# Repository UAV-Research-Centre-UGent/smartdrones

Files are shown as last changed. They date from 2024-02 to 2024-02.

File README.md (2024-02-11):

# Smartdrones
Smartdrone is an innovative UAV platform that redefines drone capabilities in educational and research settings by integrating a smartphone as the onboard computer for the drone's self-guided navigation. This approach enhances the drone's functionality not only by utilizing advanced cameras and sensors present on modern smartphones but also by taking advantage of the vast programming libraries and communication protocols available for smartphones. 

## Main features
* **Affordable:** Our design emphasizes cost-effectiveness, utilizing affordable, readily available electronic components and hardware. 
* **Open:** The platform is open and free to use. It utilizes open-source hardware and firmware. 
* **Extensible:** It is easy to integrate with various types of smartphones and sensors, ensuring adaptability to future requirements and advancements.

## Smartdrone´s architecture
Our system has three key parts: 1) The Autonomous Navigation Block (ANB) for self-flying, 2) The Manual Navigation Block (MNB) for flying it by hand using a radio, and 3) The Flight Controller Block (FCB) which manages the drone's flying mechanisms. The FCB uses sensor data to control the motors. The ANB makes the drone fly on its own using a smartphone's sensors and apps. The MNB lets a person take manual control takeover through a radio transmitter.

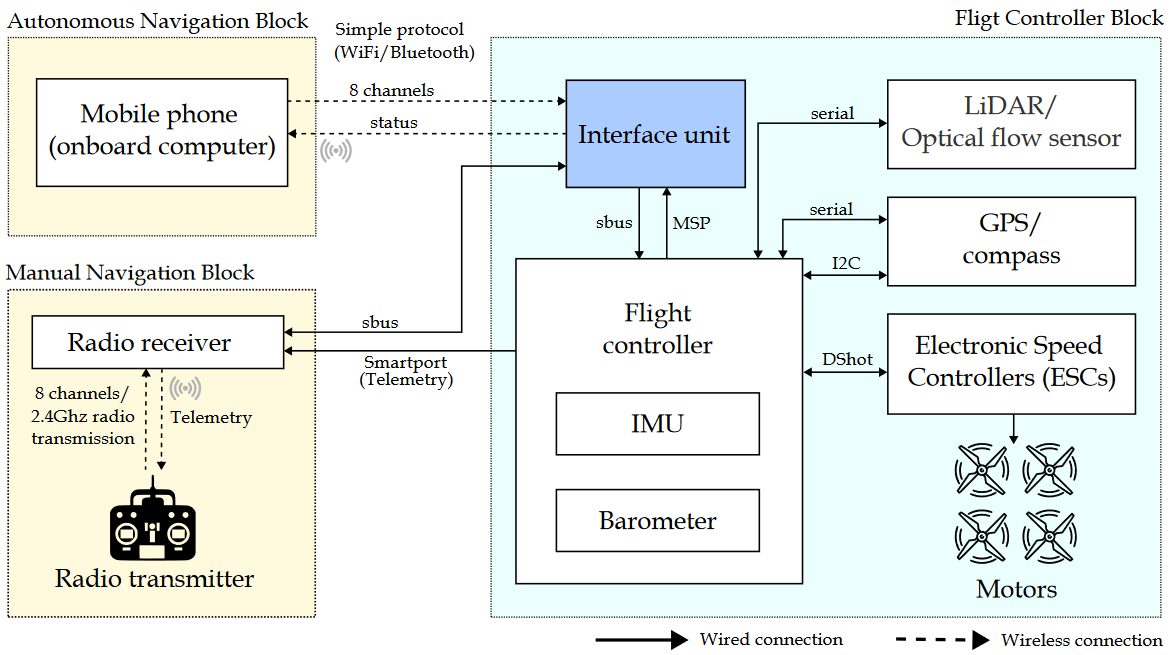
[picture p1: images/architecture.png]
Smartdone architecture


## Getting started
### Build the drone
Choose the right frame for your project. Each frame comes with recommended components, but keep in mind that not all suggested parts might be available or exactly the same. The key is to ensure that the components you select serve the same purpose or function. The folder with available frames is located in [/frames](https://github.com/UAV-Research-Centre-UGent/smartdrones/tree/main/frames). This folder contains the files for cutting the parts in carbon fiber and 3D parts that should be printed in TPU (or similar flexible filament) and PETG (or similar filament). It also provides the pins used for soldering the connections. Below is an overview of the pin connections of all the components.

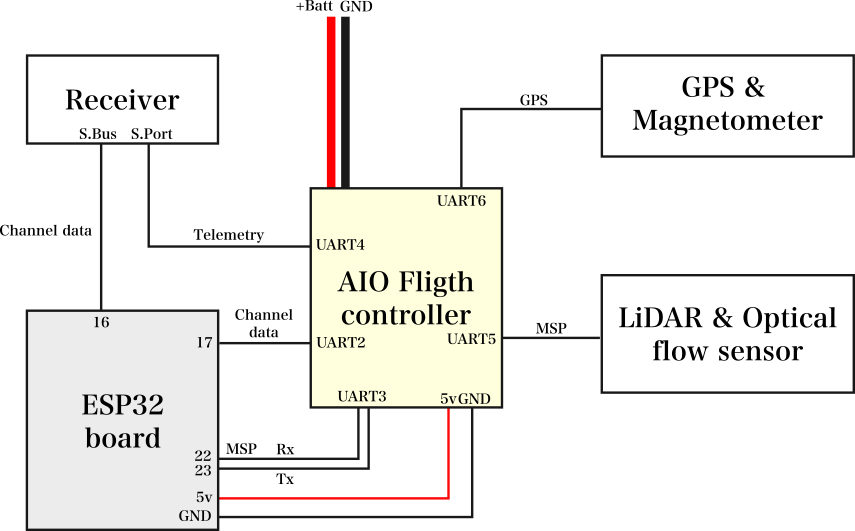
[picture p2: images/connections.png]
Connections


### Configure the drone
After installing iNAV on the flight controller, it needs to be set up correctly. The setup can vary based on the components and ports (pins) chosen on the flight controller. You'll find a document named setup.docx in the frame's folder, which explains the flight controller's configuration in detail. Below, we provide an overview of the general configuration settings.
* Ports configuration:
  * UART2: Serial (receiver)
  * UART3: MSP active (ESP32)
  * UART4: Telemetry port. Smartport.
  * UART5: MSP. Range finder and optical flow.
  * UART6: GPS.
* Receiver setup:
  * Map: TEAR.
* Modes:
  * ARM: Channel 5. Active when it is higher than 1500.
  * HORIZON, NAV ALTHOLD, NAV POSHOLD. Active when it is higher than 1500 (default).
  * BEEPER: Channel 7. Active when it is higher than 1500. 

### Transmitter
To utilize the platform, you need to pair the receiver with a compatible transmitter. The platform is compatible and has been tested with the following transmitters:
* TX16S Radio Controller (4-in-1)
* Zorro Radio Controller (4-in-1)

The basic setup is outlined below:
* Map: TEAR
* Channel 1: Throttle (THR)
* Channel 2: Elevator (ELE)
* Channel 3: Aileron (AIL)
* Channel 4: Rudder (RUD)
* Assign Channel 5 (ARM), Channel 6 (Flight Modes), Channel 7 (Enable Autonomous), and Channel 8 (Buzzer) to any available fixed switch.

### Test the drone
After setting up the drone, the next step is to conduct a test flight. This helps check if all components are correctly installed and configured and if the drone flies well. To test Smartdrones, two primary firmware options are available for installation on the ESP32.
1. [PassThrough](https://github.com/UAV-Research-Centre-UGent/smartdrones/tree/main/firmware/PassThrough): This firmware relays control commands directly from the transmitter to the drone.
2. [SimpleAutonomous](https://github.com/UAV-Research-Centre-UGent/smartdrones/tree/main/firmware/SimpleAutonomous): This firmware allows the drone to receive simple text commands from a smartphone through Bluetooth. The smartphone connects to the ESP32 via Bluetooth, sending commands that specify joystick positions and channels for basic movements.

### Tunning
While the configuration document includes recommended iNav PID settings, keep in mind these values vary for each drone. If the drone vibrates too much or is unstable during flight, you can adjust its performance by modifying the PID values. For guidance on how to do this, check out the video playlist at: [iNAV configuration guide](https://www.youtube.com/playlist?list=PLOUQ8o2_nCLloACrA6f1_daCjhqY2x0fB).

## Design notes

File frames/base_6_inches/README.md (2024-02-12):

# Base frame (5-6 inches)
This frame is designed to carry out smartphones with screen sizes up to 6.5 inches. When assembled with the suggested components and powered by a 2000 mAh 4S battery, the drone is able to achieve a flight duration ranging from 10 to 15 minutes.

## Components
This is the list of recommended components. 
- [GOKU HD 745 EVO 40A AIO](https://flywoo.net/products/goku-hd745-evo-40a-aio-bl_32-dji-plus-play)
- [iFlight M8Q-5883-GPS Module V2.0](https://newbeedrone.com/products/iflight-m8q-5883-gps-and-compass-v2-0)
- [Matek 3901-L0X](http://www.mateksys.com/?portfolio=3901-l0x)
- [FrSky R-XSR](https://www.frsky-rc.com/product/r-xsr/)
- [T-Motor F2203.5 - 1500KV](https://store.tmotor.com/product/f2203_5-fpv-motor.html) 
- [ESP32 Development Board](https://www.espressif.com/en/products/devkits/esp32-devkitc)
- [Gemfan F6030](https://www.getfpv.com/gemfan-floppy-proppy-f6030-3-blade-propeller-set-of-4.html)

## Assembly the frame
The drone construction is based on a carbon fiber Frame, which is fastened using screws, secure nuts, and aluminum standoffs. The design files for each carbon fiber part can be found in the [frame](frame) folder, provided in DXF format for precision manufacturing. Below is a detailed breakdown of the parts that constitute the frame, including the thickness of each carbon fiber component:
* Top Plate: 1.5mm thick
* Bottom Plate: 2mm thick
* Front Arm: 6mm thick
* Rear Arm: 6mm thick
* Arm Holder: 2mm thick
* Aluminum Standoffs: 25mm in length
* M3 Bolts and Nuts: 12mm in size

An illustrative guide detailing the assembly of the frame is provided in the image below. 
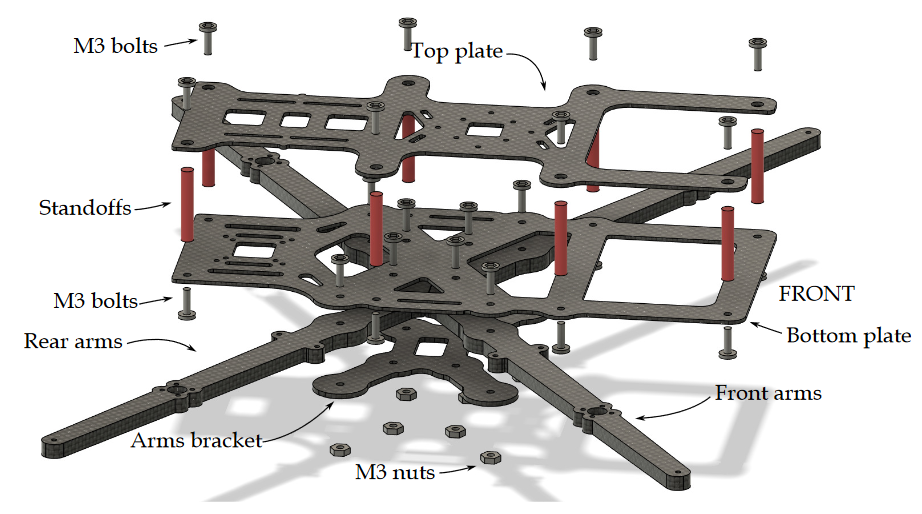
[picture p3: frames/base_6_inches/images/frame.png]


## 3D printed parts
The drone frame includes parts that need to be printed using a 3D printer. The files for these specific parts are in the [3dparts](3dparts) folder. Below, we provide a detailed list of the components to be printed, along with the recommended type of filament for each. 
* [Front bumper](3dparts/tpu-front_bumper.stl) (TPU-95-98A) 
* [Landing foot](3dparts/tpu-landing_foot.stl) (TPU-95-98A)
* [Battery holder](3dparts/tpu-battery_holder.stl) (TPU-95-98A)
* [LiDAR mount](3dparts/tpu-lidar_mount.stl) (TPU-95-98A)
* [Antenna holder (left)](3dparts/tpu-antenna_holder_left.stl) (TPU-95-98A)
* [Antenna holder (right)](3dparts/tpu-antenna_holder_right.stl) (TPU-95-98A)
* [Antenna tip](3dparts/tpu-antenna_tip.stl) (TPU-95-98A)
* [ESP32 holder](3dparts/petg-esp32_holder.stl) (PETG)
* [Flight controller protector](3dparts/petg-fc_protector.stl) (PETG)
* [Front duct (left)](3dparts/petg-duct_front_left.stl) (PETG)
* [Front duct (right)](3dparts/petg-duct_front_right.stl) (PETG)
* [Rear duct (left)](3dparts/petg-duct_rear_left.stl) (PETG)
* [Rear duct (left)](3dparts/petg-duct_rear_right.stl) (PETG)

The location of the 3D printed parts are shown in the following image: 
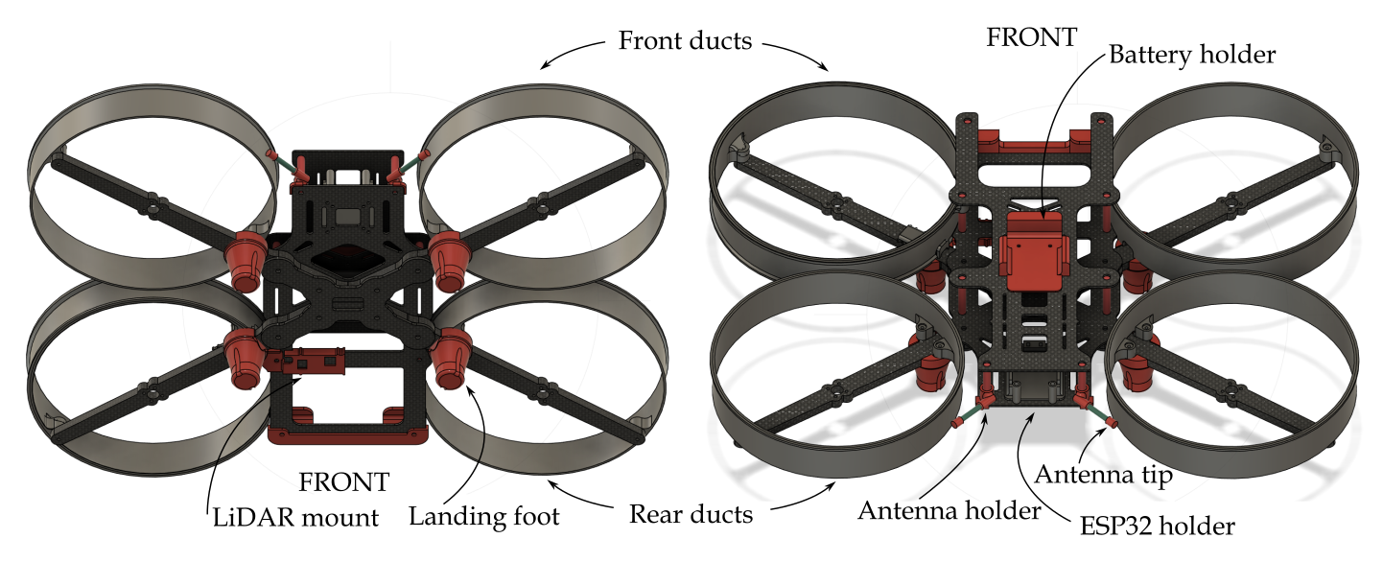
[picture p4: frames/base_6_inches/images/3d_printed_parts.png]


In addition to the parts already mentioned, your drone build will require some additional components and hardware not previously listed. These include 20mm M2 screws and nuts, which are used for securing the ducts. You will also need battery straps to ensure both the smartphone and the battery are firmly held in place.

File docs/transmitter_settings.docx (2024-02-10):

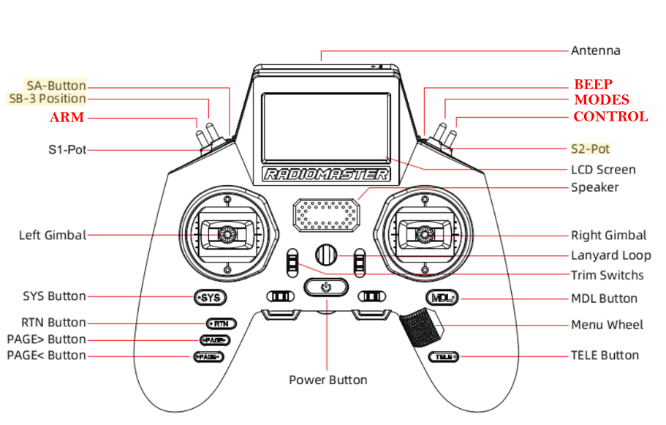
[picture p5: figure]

Cheat sheet

THROTTLE (T) | Channel 1
PITCH | Channel 2
ROLL | Channel 3
YAW | Channel 4
ARM | Channel 5 | Arm the drone
MODES | Channel 6 | Change the modes
CTRL | Channel 7 | Leave/take control (do not used by iNAV)
BEEP | Channel 8 | Beeping

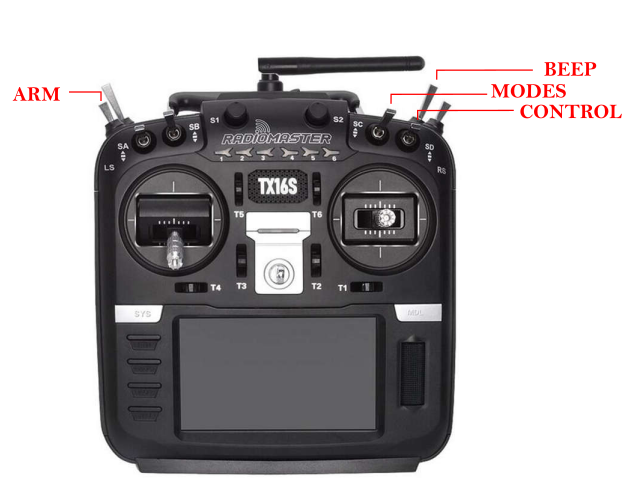
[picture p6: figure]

Values for channels

MIN_SBUS_VALUE | 172
MAX_SBUS_VALUE | 1811
MID_SBUS_VALUE | 992

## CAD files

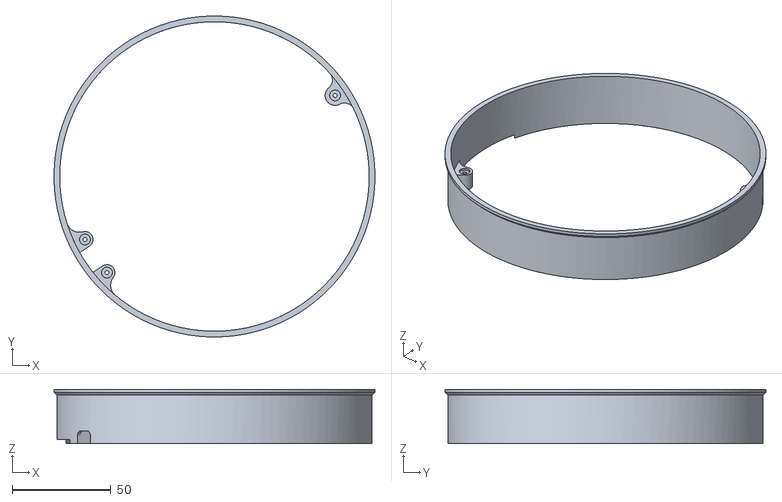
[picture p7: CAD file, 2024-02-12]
frames/base_6_inches/3dparts/petg-duct_front_right.stl
162.2 x 162.2 x 27.5

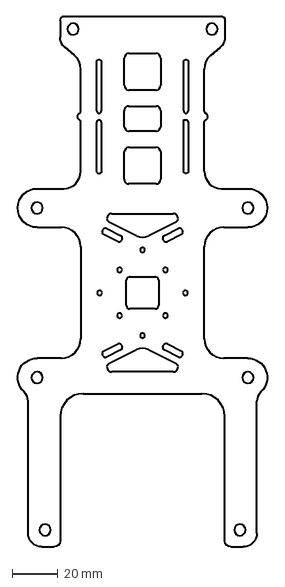
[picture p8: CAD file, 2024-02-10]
frames/base_6_inches/frame/top_plate.dxf
110.4 x 232.0 mm

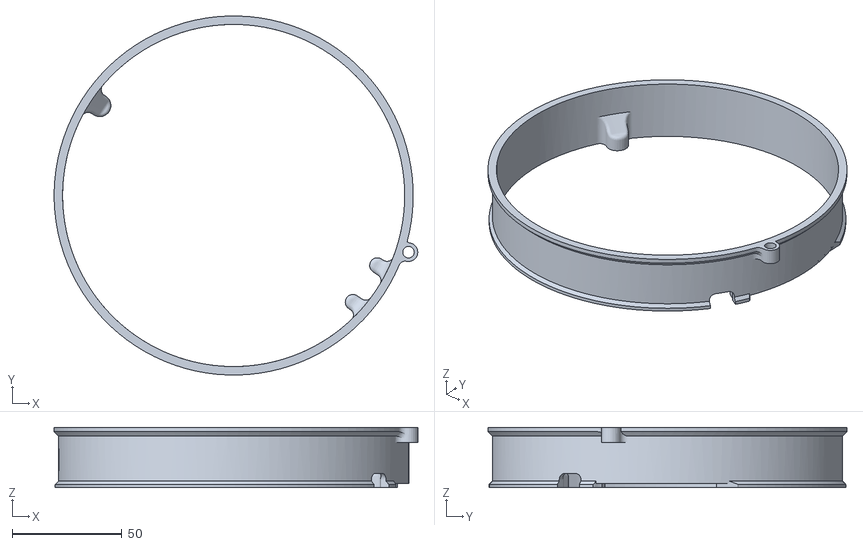
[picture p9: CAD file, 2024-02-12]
frames/base_6_inches/3dparts/petg-duct_front_left.stl
165.6 x 163.5 x 27.5

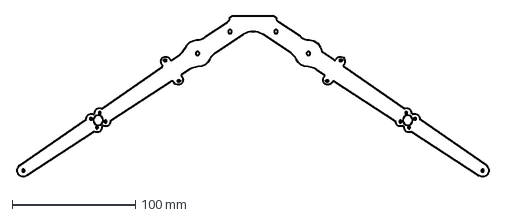
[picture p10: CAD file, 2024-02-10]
frames/base_6_inches/frame/front_arm.dxf
384.6 x 130.9 mm

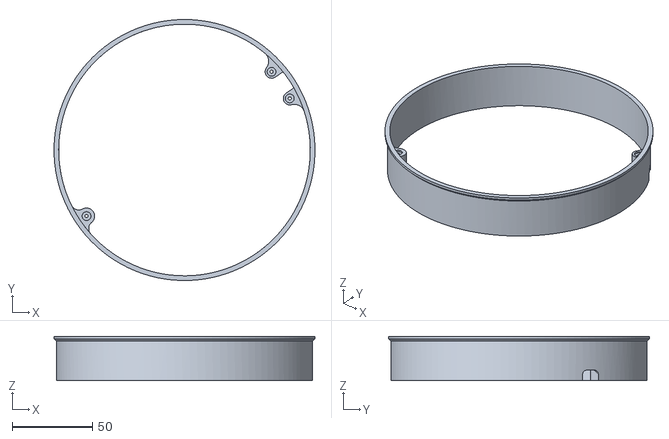
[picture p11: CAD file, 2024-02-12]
frames/base_6_inches/3dparts/petg-duct_rear_left.stl
162.2 x 162.2 x 27.5

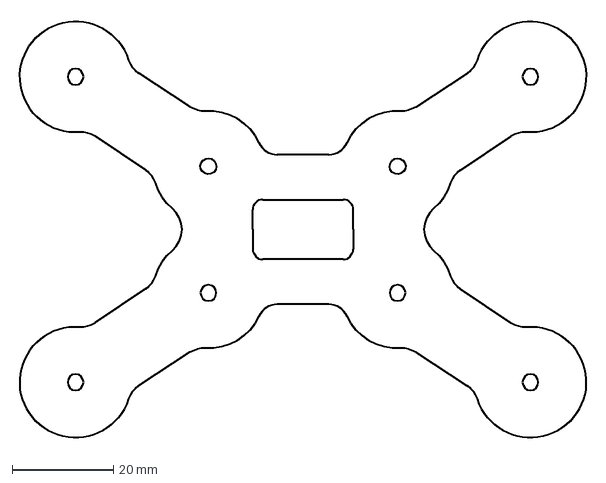
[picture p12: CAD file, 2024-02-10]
frames/base_6_inches/frame/arm_holder.dxf
113.5 x 84.5 mm

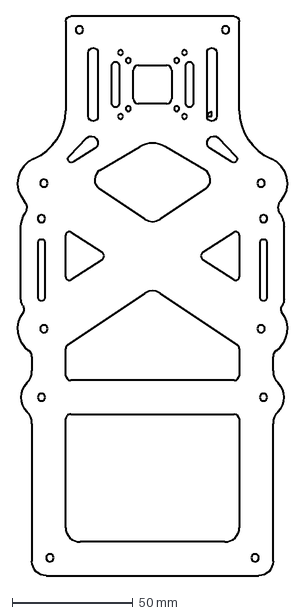
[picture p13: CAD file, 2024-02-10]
frames/base_6_inches/frame/bottom_plate.dxf
113.0 x 232.0 mm

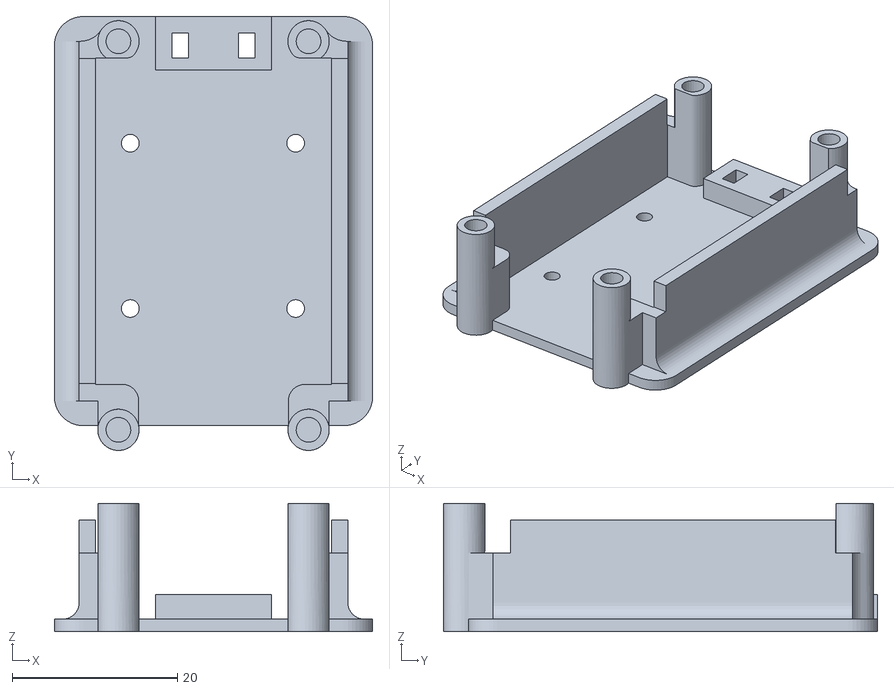
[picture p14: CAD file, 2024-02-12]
frames/base_6_inches/3dparts/petg-esp32_holder.stl
38.5 x 52.5 x 15.5

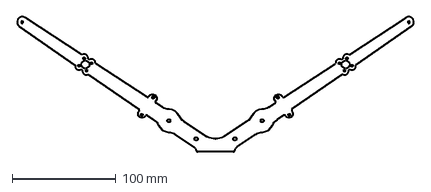
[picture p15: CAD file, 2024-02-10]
frames/base_6_inches/frame/rear_arm.dxf
384.6 x 130.9 mm

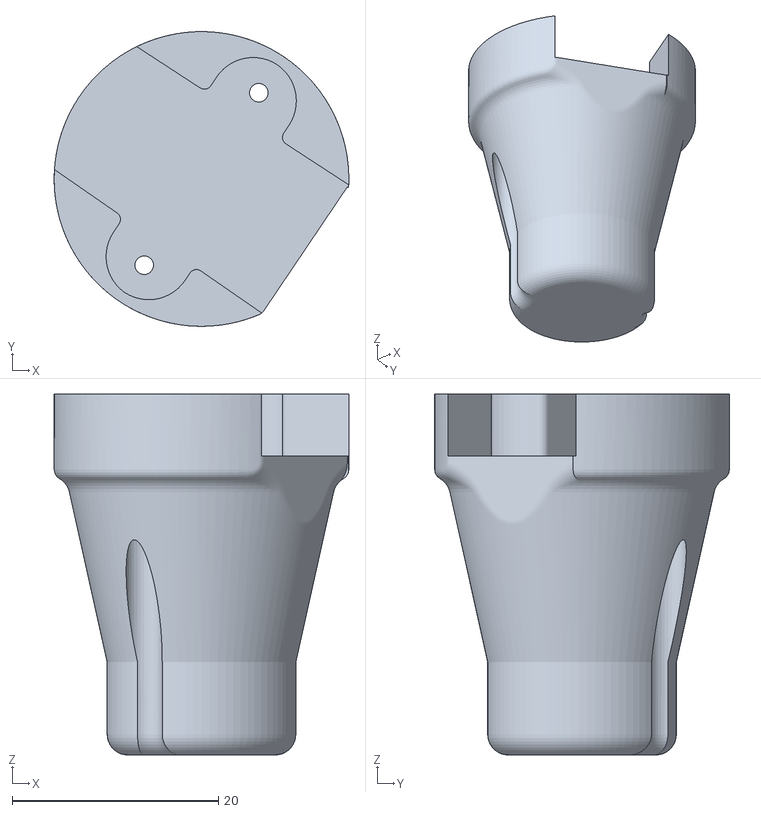
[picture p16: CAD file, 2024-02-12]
frames/base_6_inches/3dparts/tpu-landing_foot.stl
28.6 x 28.6 x 35.0

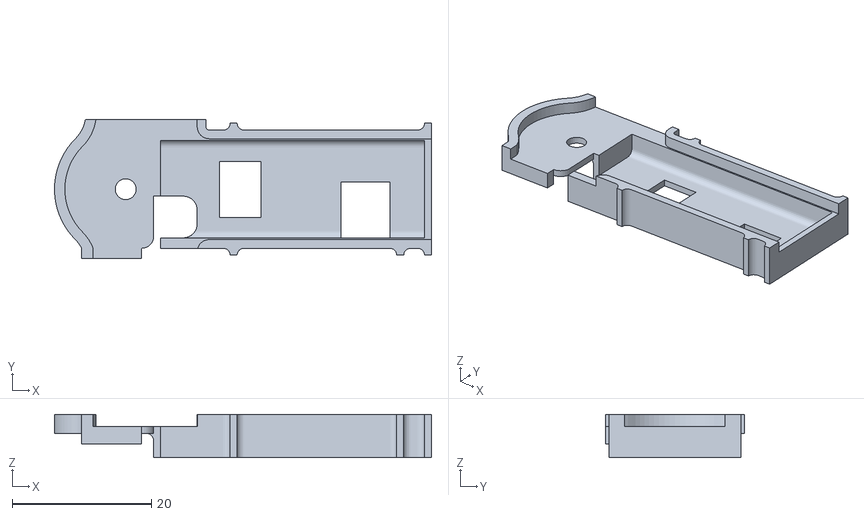
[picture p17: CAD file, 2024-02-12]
frames/base_6_inches/3dparts/tpu-lidar_mount.stl
54.2 x 20.1 x 6.25

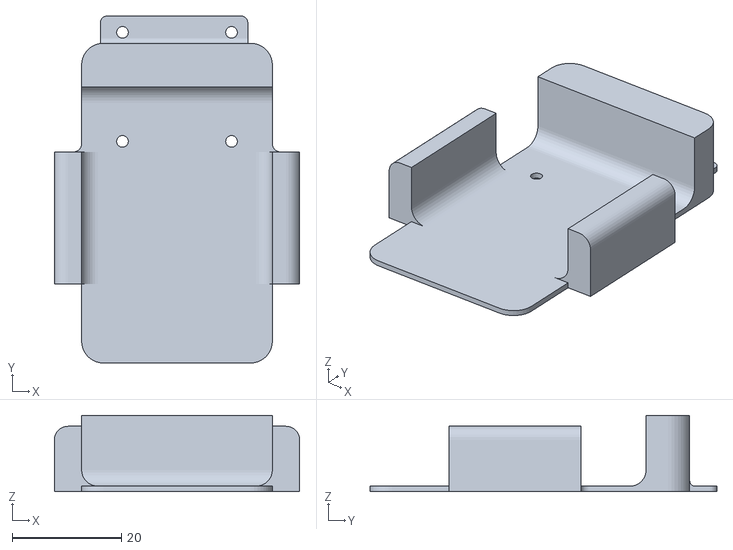
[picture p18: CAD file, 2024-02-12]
frames/base_6_inches/3dparts/tpu-battery_holder.stl
45.0 x 63.6 x 14.0

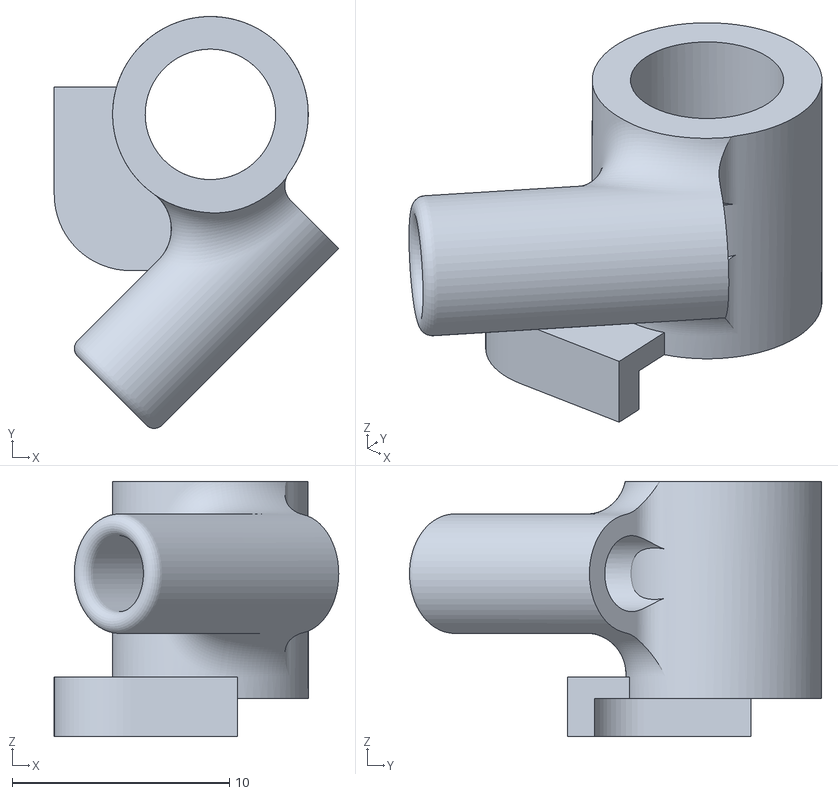
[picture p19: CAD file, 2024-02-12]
frames/base_6_inches/3dparts/tpu-antenna_holder_left.stl
13.1 x 18.9 x 11.8

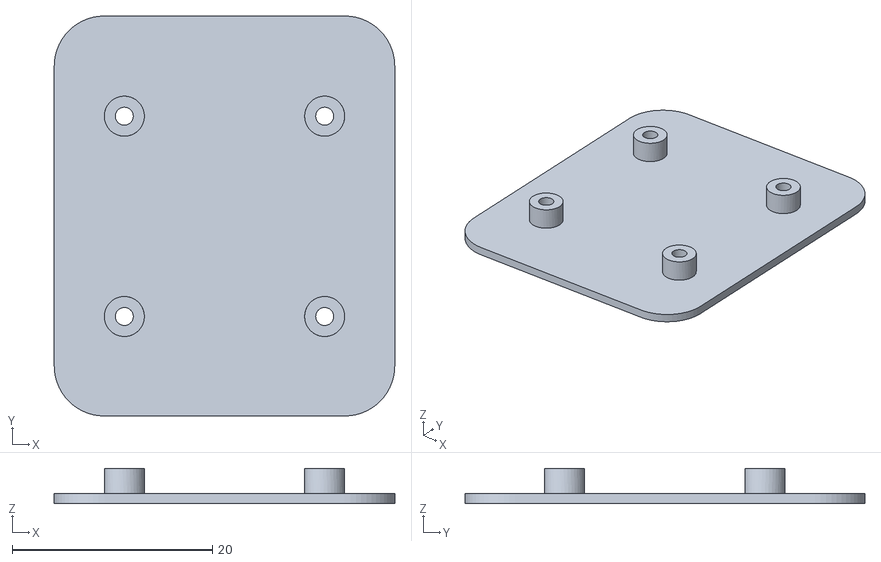
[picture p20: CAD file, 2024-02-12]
frames/base_6_inches/3dparts/petg-fc_protector.stl
34.0 x 39.9 x 3.50

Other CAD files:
frames/base_6_inches/3dparts/petg-duct_rear_right.stl
frames/base_6_inches/3dparts/tpu-antenna_holder_right.stl
frames/base_6_inches/3dparts/tpu-front_bumper.stl
frames/base_6_inches/3dparts/tpu-antenna_tip.stl

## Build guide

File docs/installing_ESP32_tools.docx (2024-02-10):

# Installing ESP32 Add-on in Arduino IDE

To install the ESP32 board in your Arduino IDE, follow these next instructions:

In your Arduino IDE, go to File> Preferences

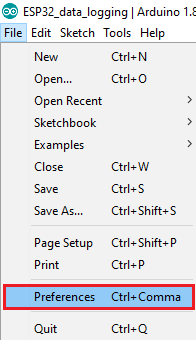
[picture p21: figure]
Installing ESP32 Add-on in Arduino IDE Windows, Mac OS X, Linux open preferences

Enter https://dl.espressif.com/dl/package_esp32_index.json into the “Additional Board Manager URLs” field as shown in the figure below. Then, click the “OK” button:

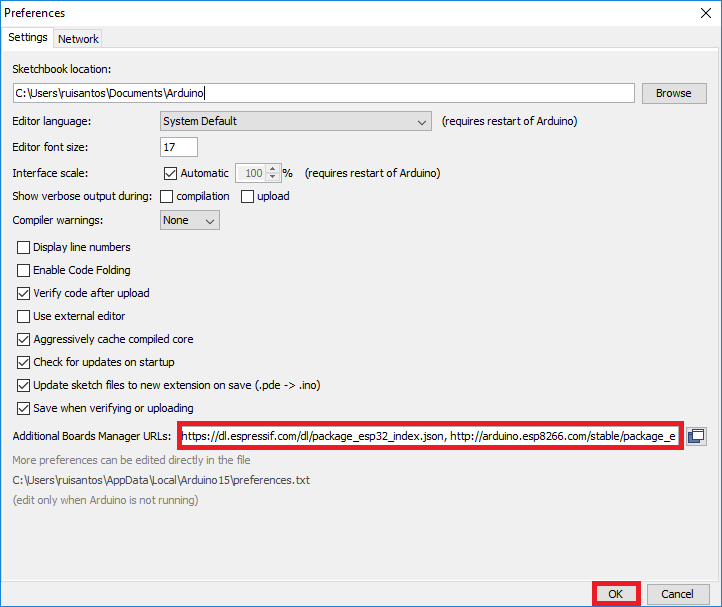
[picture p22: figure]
Installing ESP32 Add-on in Arduino IDE Windows, Mac OS X, Linux enter URLs

Note: if you already have the ESP8266 boards URL, you can separate the URLs with a comma as follows:

https://dl.espressif.com/dl/package_esp32_index.json, http://arduino.esp8266.com/stable/package_esp8266com_index.json

Open the Boards Manager. Go to Tools > Board > Boards Manager…

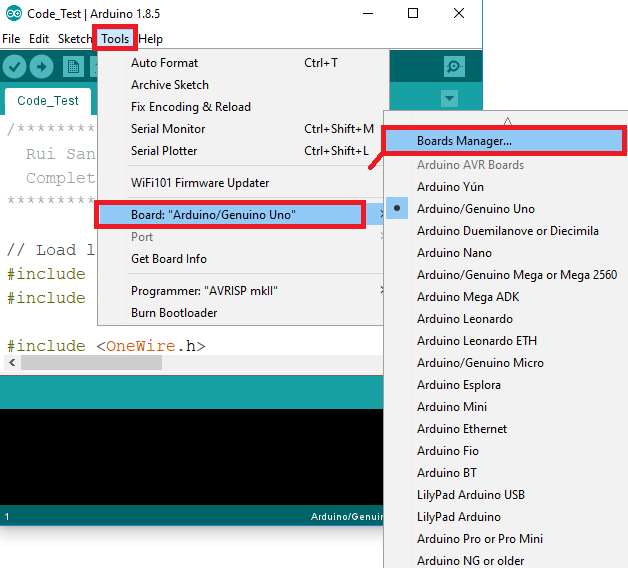
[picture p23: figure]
Installing ESP32 Add-on in Arduino IDE Windows, Mac OS X, Linux open boards manager

Search for ESP32 and press install button for the “ESP32 by Espressif Systems“:

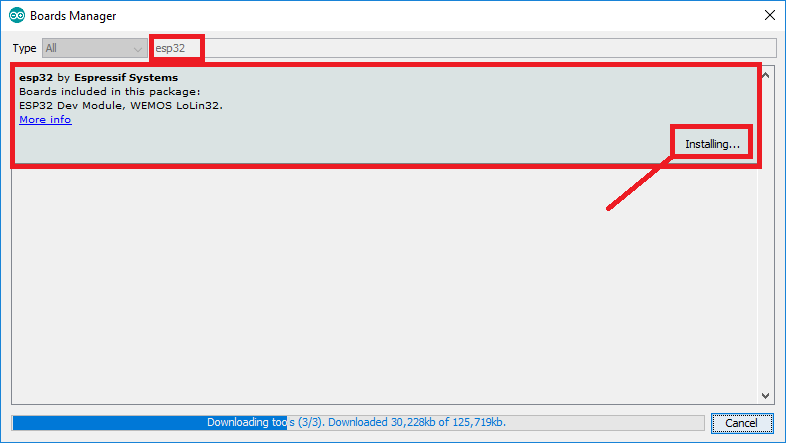
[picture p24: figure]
ESP32 Add-on in Arduino IDE Windows, Mac OS X, Linux Installed

That’s it. It should be installed after a few seconds.

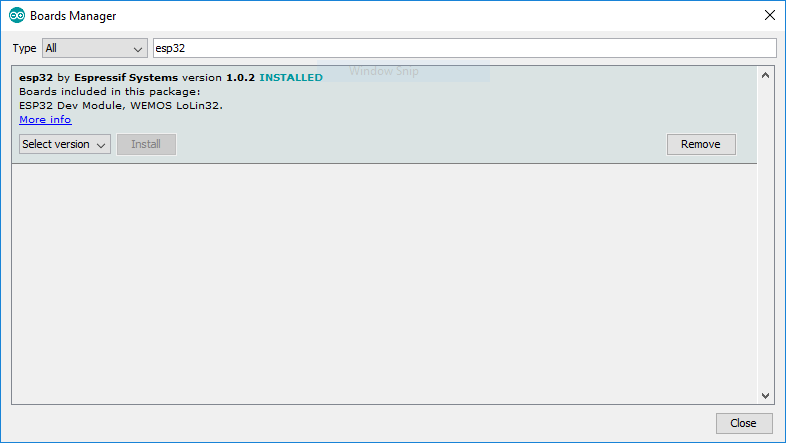
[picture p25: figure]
ESP32 Board add-on in Arduino IDE installed

# Testing the Installation (optional)

Plug the ESP32 board to your computer. With your Arduino IDE open, follow these steps:

1. Select your Board in Tools > Board menu (in my case it’s the DOIT ESP32 DEVKIT V1)

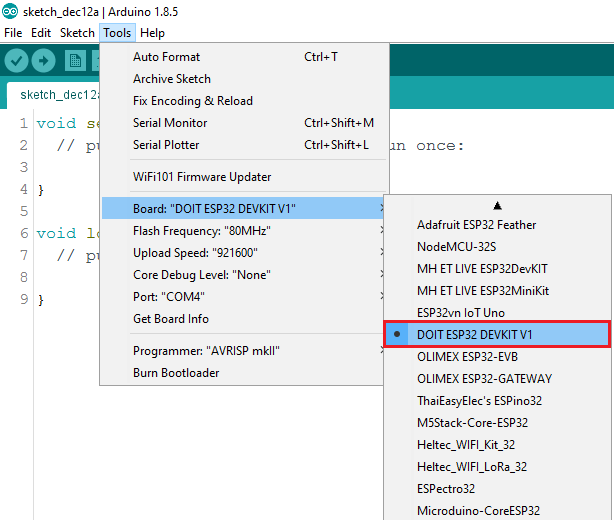
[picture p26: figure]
Arduino IDE select the ESP32 board in Tools menu

2. Select the Port (if you don’t see the COM Port in your Arduino IDE, you need to install the CP210x USB to UART Bridge VCP Drivers (https://www.silabs.com/products/development-tools/software/usb-to-uart-bridge-vcp-drivers)):

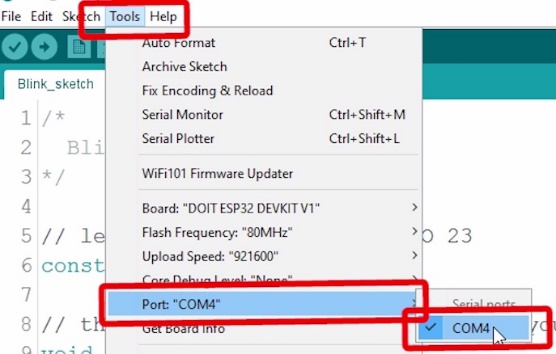
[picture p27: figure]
Arduino IDE select the ESP32 Port in Tools menu

3. Open the following example under File > Examples > WiFi (ESP32) > WiFiScan

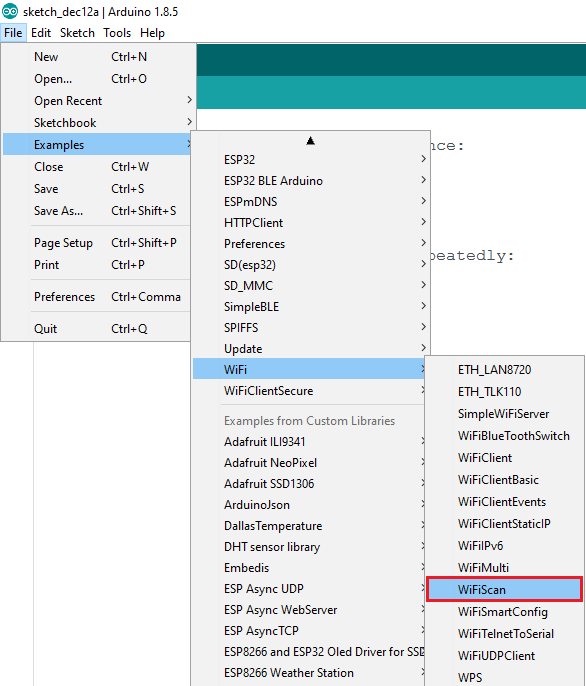
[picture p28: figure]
Arduino IDE open WiFiScan example for ESP32

4. A new sketch opens in your Arduino IDE:

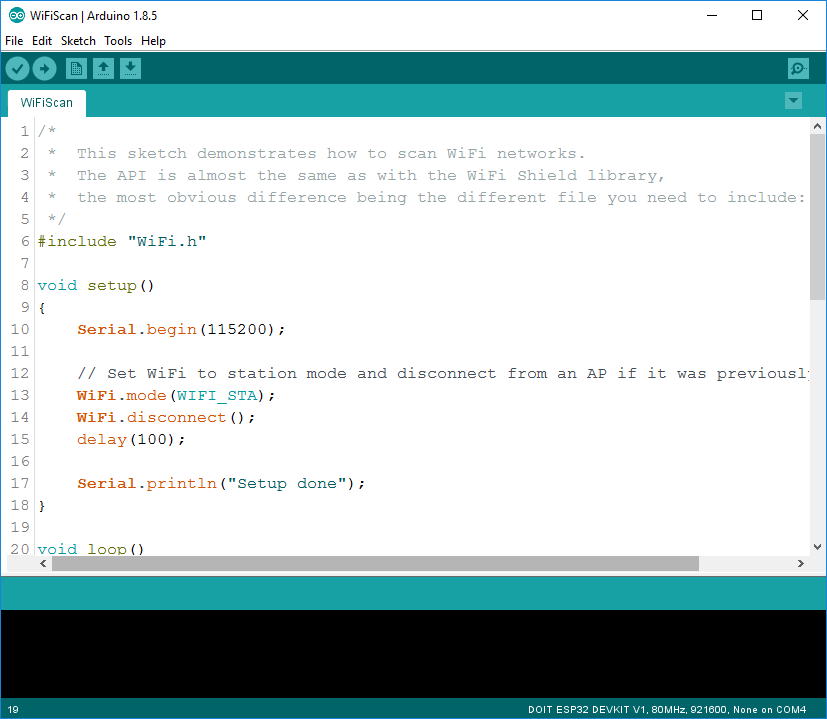
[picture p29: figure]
Arduino IDE uploading WiFiScan example to ESP32

5. Press the Upload button in the Arduino IDE. Wait a few seconds while the code compiles and uploads to your board.

6. If everything went as expected, you should see a “Done uploading.” message.

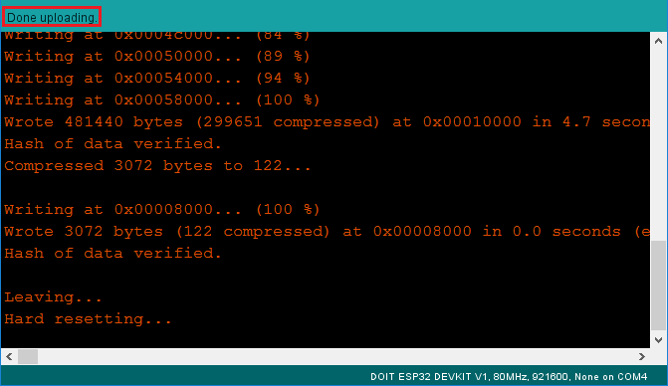
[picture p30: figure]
Arduino IDE done uploading ESP32 WiFiScan sketch

7. Open the Arduino IDE Serial Monitor at a baud rate of 115200:

8. Press the ESP32 on-board Enable button and you should see the networks available near your ESP32:

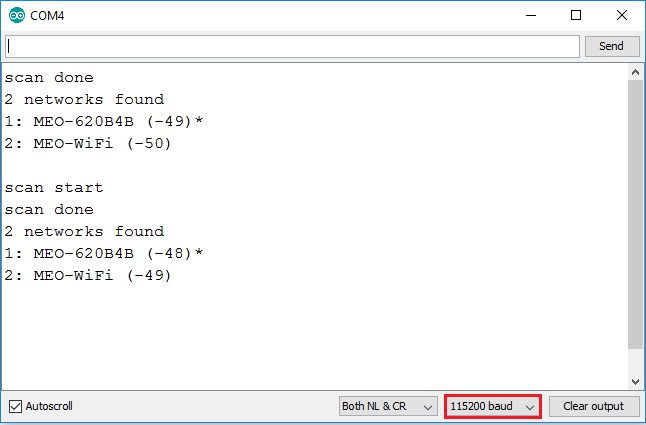
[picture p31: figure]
ESP32 Testing Add-on installation in Windows PC, Max OS X, and Linux computer

# Installing libraries

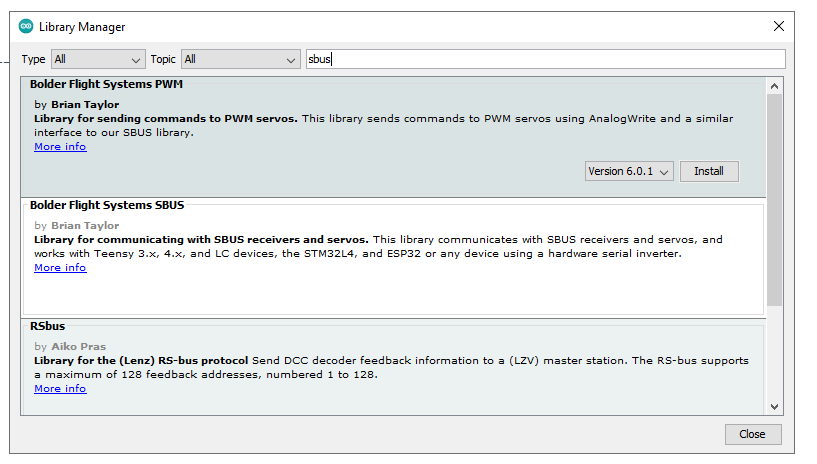
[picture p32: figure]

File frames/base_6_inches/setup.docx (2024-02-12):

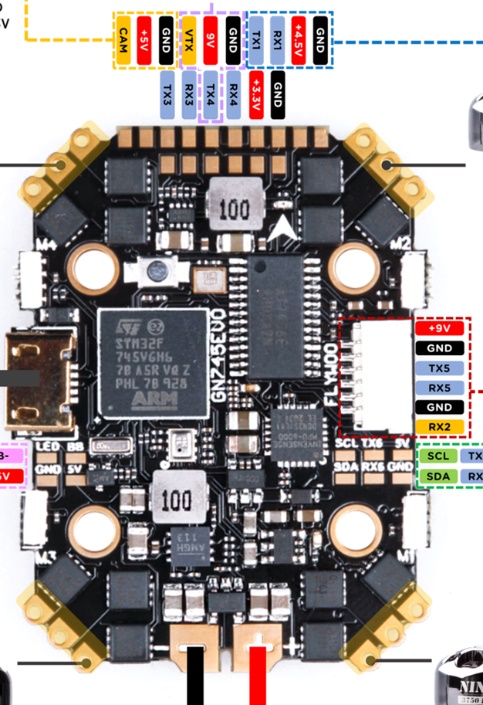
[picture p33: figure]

# Port and pads connections

UART1 | Free
UART2 | Receiver signal (ESP32)
UART3 | MSP signal (ESP32)
UART4 | Telemetry
UART5 | Optical flow & Lidar sensors
UART6 | GPS
UART7 | ESC telemetry (built-in)

# PINS

Connect all the components using the ports defined in the following diagram:

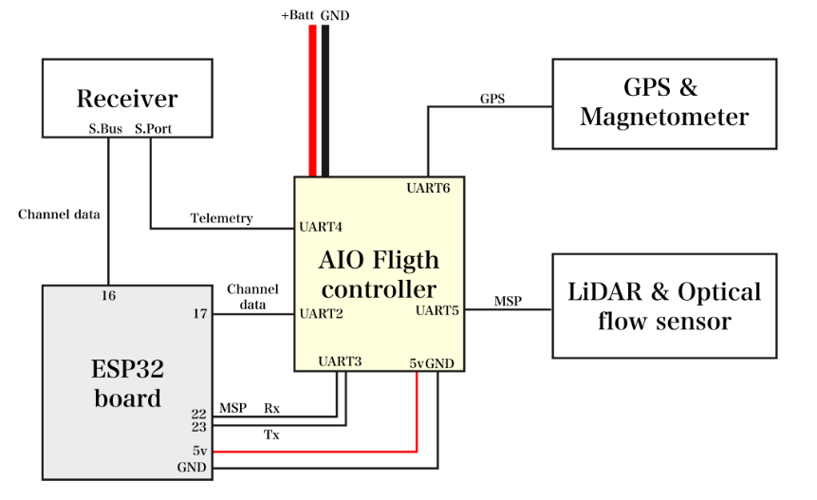
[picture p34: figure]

# Configuration in iNav

Installing iNav using iNav configuration (https://github.com/iNavFlight/inav-configurator/releases).

Then flash the firmware to the flight controller. Finally connect the battery and check if all the sensors are recognized as follows:

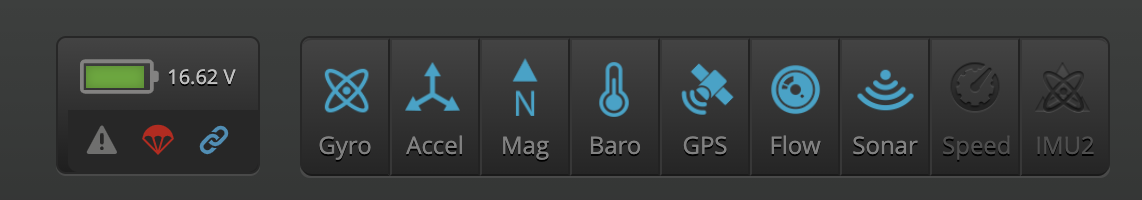
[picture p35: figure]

Calibrate the accelerometer, compass, and optical flow sensors. This calibration step needs to be repeated the first time the firmware is installed on the FC or if the GPS (with compass) or the optical flow sensors are moved or changed.

Verify that all the sensors are configured as below:

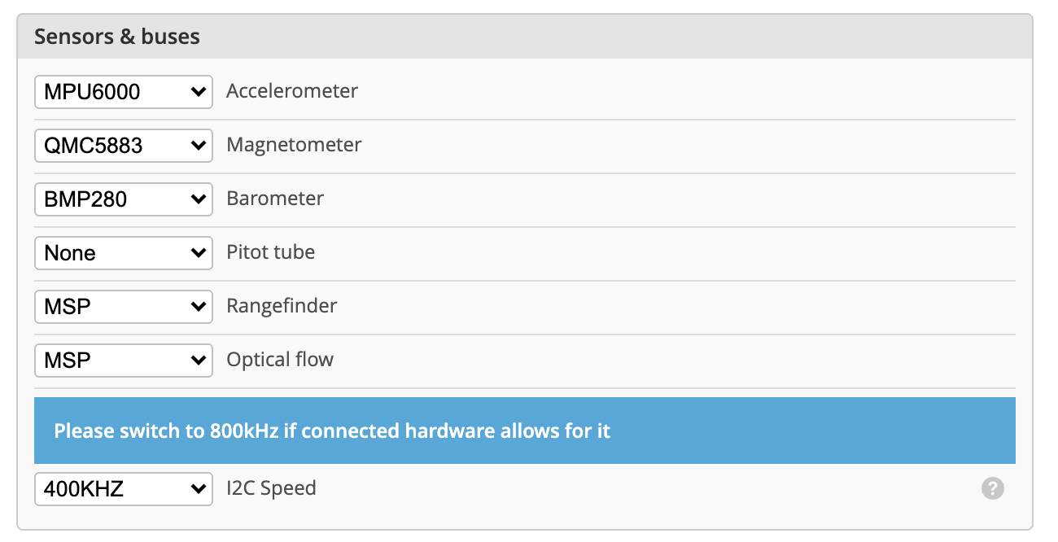
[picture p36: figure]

## iNav operation

The key sensor for INAV is an accelerometer. Measured acceleration is translated from body-fixed frame to local NEU coordinates and integrated to yield velocities in North, East and Up directions. Velocity is further integrated to produce coordinates.

As accelerometer tend to drift, estimated velocities and coordinates tend to drift as well. This accumulated error is corrected from various reference sources - GPS, BARO, SONAR. Position estimator also maintains estimated position error for horizontal (X-Y) and vertical (Z) position.

When reference source is not available for some reason, estimated position error increases until it reaches a certain threshold. Beyond that threshold position is no longer updated and marked invalid until a valid reference source is available again. This allows, for example, to fly through short (measured in seconds) GPS outages.

Using multiple sensors for estimation allows to filter noisy data (e.g. from barometer), interpolate between rare readings (e.g. from GPS), and immediately react on fast motion changes (using accelerometers) in the same time.

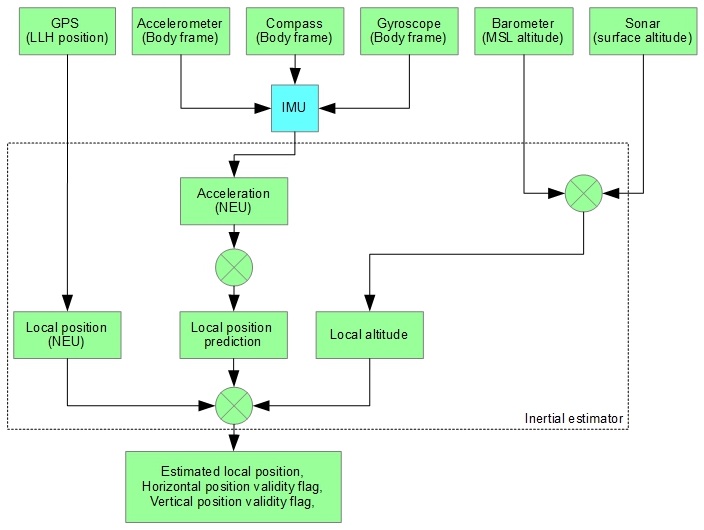
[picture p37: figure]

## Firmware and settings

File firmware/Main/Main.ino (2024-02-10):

//**** Includes
#include "BluetoothSerial.h"
#include "Constants.h"
#include "HardwareConfig.h"
#include "MSP.h"
#include "sbus.h"

//**** Tasks
TaskHandle_t mainTask;
TaskHandle_t mspTask;

//**** SBus setup
bfs::SbusRx sbus_rx(&Serial1);
bfs::SbusTx sbus_tx(&Serial1);

//**** BT setup
#if !defined(CONFIG_BT_ENABLED) || !defined(CONFIG_BLUEDROID_ENABLED)
#error Bluetooth is not enabled! Please run `make menuconfig` to and enable it
#endif

//**** Variables
BluetoothSerial SerialBT;

//**** Drone data
int32_t altitude = 0; //Altitude in centimeters
uint8_t drone_vbat = 0; //Main analog voltage (from the battery pads)
uint16_t drone_mah = 0;
// Raw data
// To convert these data into pitch,roll,yaw data: 
// https://engineering.stackexchange.com/questions/3348/calculating-pitch-yaw-and-roll-from-mag-acc-and-gyro-data
int16_t drone_gyro[3]={0,0,0};
int16_t drone_acc[3]={0,0,0};
int16_t drone_mag[3]={0,0,0};

// Status
uint8_t system_status = WAITING_FOR_DEVICES;
uint8_t drone_status = DRONE_DISARMED;
uint8_t flight_mode = MANUAL_MODE;
uint8_t bt_status = BT_DISCONNECTED;
uint8_t rc_status = RC_DISCONNECTED;

// Decoded channel information from SBUS and BT
static std::array<int16_t, bfs::SbusRx::NUM_CH()> channels;
// Bluetooth data frame
static std::array<int16_t, BT_DATA_FRAME_SIZE> bt_data;
static std::array<int16_t, NUM_CHANNELS> bt_channels;
// SBus data frame
std::array<int16_t, bfs::SbusRx::NUM_CH()> sbus_data;

// Communication with the FC using MSP protocol
MSP msp;

void setup() {

  Serial.begin(BAUDRATE);

  //**** Waiting for serial
  while (!Serial) {
  }

  //**** Init hardware pins
  InitHardwarePins();

  // ---- Bluetooth
  bluetooth_init();
  delay(500);

  // Begin the SBUS communication
  sbus_rx.Begin(SBUS_RXPIN, SBUS_TXPIN);
  sbus_tx.Begin(SBUS_RXPIN, SBUS_TXPIN);
#ifdef USE_SERIAL_OUTPUT
  Serial.println("Receiver device started");
#endif
  resetChannels();
  sendChannelsData(); // Prevent randon values being sent to the FC
  delay(500);

  //****  MSP communication
  Serial2.begin(MSP_BAUDRATE, SERIAL_8N1, MSP_RXPIN, MSP_TXPIN);
  msp.begin(Serial2);

  //**** All ready
#ifdef USE_SERIAL_OUTPUT
  Serial.println("The device started.. Waiting connections");
#endif

  //**** Task to control loops
  xTaskCreatePinnedToCore(
      mainLoop,   /* Task function. */
      "mainLoop", /* name of task. */
      10000,      /* Stack size of task */
      NULL,       /* parameter of the task */
      1,          /* priority of the task */
      &mainTask,  /* Task handle to keep track of created task */
      0);         /* pin task to core 0 */
  delay(500);

  // create a task that will be executed in the Task2code() function, with
  // priority 1 and executed on core 1
  xTaskCreatePinnedToCore(
      mspLoop,   /* Task function. */
      "mspLoop", /* name of task. */
      10000,     /* Stack size of task */
      NULL,      /* parameter of the task */
      1,         /* priority of the task */
      &mspTask,  /* Task handle to keep track of created task */
      1);        /* pin task to core 1 */
  delay(500);
}

//**** Send channels data to the FC
void sendChannelsData() {
  sbus_tx.ch(channels);
  sbus_tx.Write();
}

// Call back to check if the bluetooth was disconnected
void callback(esp_spp_cb_event_t event, esp_spp_cb_param_t *param) {
  if (event == ESP_SPP_SRV_OPEN_EVT) {
    bt_status = BT_CONNECTED;
    Serial.println("FCOM (Bluetooth) is connected");
  }
  if (event == ESP_SPP_CLOSE_EVT) {
    bt_status = BT_DISCONNECTED;
    Serial.println("FCOM (Bluetooth) is disconnected");
  }
}

//**** Init bluetooth
void bluetooth_init() {
  if (!SerialBT.begin(AIRCRAFT_NAME)) {
#ifdef USE_SERIAL_OUTPUT
    Serial.println("Bluetooth device can not be initialized");
#endif
  } else {
#ifdef USE_SERIAL_OUTPUT
    Serial.println("Bluetooth device started");
#endif
    SerialBT.register_callback(callback);
  }
  // Set all data lo low values
  initRCBTData();
}

// Copy SBus data to channel, this is mainly for visualize the data
void sBUSToChannel() {
  for (int i = 0; i < bfs::SbusRx::NUM_CH(); i++) {
    channels[i] = sbus_data[i];
  }
}

int32_t getBaroAltitude() {
  msp_altitude_t alt;
  if (msp.request(MSP_ALTITUDE, &alt, sizeof(alt))) {
    return alt.estimatedActualPosition;
  }
  return MSP_INT32_ERROR;
}

// Check is the aircraft is ready to flight
// Check list:
// - Bluetooth connection
// - Radio connection (not in failsafe)
// - TODO:
// - MSP connection
// - AIRCRAFT ready (GPS fixed, all devices working properlly)
void checkConnectionStatus() {
  if (system_status == READY_TO_FLIGHT) {
    if ((bt_status == BT_DISCONNECTED || bt_status == BT_ERROR) &&
        (rc_status == RC_DISCONNECTED || rc_status == RC_FAILSAFE)) {
      // This is a failsafe mode
      if (system_status != FAILSAFE) {
        Serial.println(
            "Failsafe mode enabled.. Drone lost BT and RC connections!!");
      }
      system_status = FAILSAFE;
    }
  }
  if (bt_status == BT_CONNECTED && rc_status == RC_CONNECTED) {
    if (system_status != READY_TO_FLIGHT) {
      system_status = READY_TO_FLIGHT;
      Serial.println("Devices connected.. Drone is ready to flight.");
    }
  }
}

// Check flight mode selection based on the MODE channel from the transmitter
// (manual) Flight mode can be change from the transmitter
void checkFlightMode(int value) {
  // Flight mode status
  if (value < MID_SBUS_VALUE && flight_mode != MANUAL_MODE) {
    flight_mode = MANUAL_MODE;
    Serial.println("Manual mode enabled");
  } else if (value > MID_SBUS_VALUE && flight_mode != AUTONOMOUS_MODE) {
    flight_mode = AUTONOMOUS_MODE;
    Serial.println("Autonomous mode enabled");
  }
}

//**** Update drone status from FC
void updateDroneTelem() {
  msp_sonar_altitude_t sonar_alt;
  msp_analog_t adata;
  msp_raw_imu_t imu_data;
  msp_altitude_t baro_alt;
  // Update data only when is correct

  if (msp.request(MSP_ALTITUDE, &baro_alt, sizeof(baro_alt))) {
    altitude =  baro_alt.estimatedActualPosition;
  }
  // if (msp.request(MSP_SONAR_ALTITUDE, &sonar_alt, sizeof(sonar_alt))) {
  //   altitude = sonar_alt.altitude; // int32_t
  // }
  // if (msp.request(MSP_ANALOG, &adata, sizeof(adata))){
  //   drone_vbat = adata.vbat;
  //   drone_mah = adata.mAhDrawn;
  // }
  // if (msp.request(MSP_RAW_IMU, &imu_data, sizeof(imu_data))){
  //   //Gyro data
  //   drone_gyro[0]=imu_data.gyro[0];
  //   drone_gyro[1]=imu_data.gyro[1];
  //   drone_gyro[2]=imu_data.gyro[2];
  //   //Acc
  //   drone_acc[0]=imu_data.acc[0];
  //   drone_acc[1]=imu_data.acc[1];
  //   drone_acc[2]=imu_data.acc[2];
  //   //Mag
  //   drone_mag[0]=imu_data.mag[0];
  //   drone_mag[1]=imu_data.mag[2];
  //   drone_mag[2]=imu_data.mag[2];
  // }




  // if (msp.request(MSP_ANALOG, &adata, sizeof(adata))) {
  //   voltage = adata.vbat;
  //   rssi = adata.rssi;
  // }
}

//**** Init BT data properly
void initRCBTData() {
  // Min throtle
  bt_data[THROTTLE] = MIN_SBUS_VALUE;
  // All in the middle
  bt_data[PITCH] = MID_SBUS_VALUE;
  bt_data[ROLL] = MID_SBUS_VALUE;
  bt_data[YAW] = MID_SBUS_VALUE;
  // Disarmed
  bt_data[AUX1] = MIN_SBUS_VALUE;
  // Autonomous mode ON
  bt_data[AUX2] = MIN_SBUS_VALUE;
  // All the rest in low position
  bt_data[AUX3] = MAX_SBUS_VALUE;
  // bt_data[BEEP]=MIN_SBUS_VALUE;
}

// Shoe channel values on serial USB out
void showChannelValues() {

  // Serial.print(" T:");
  // Serial.println(channels[THROTTLE]);
  // Serial.print(" P:");
  // Serial.println(channels[PITCH]);
  // Serial.print(" R:");
  // Serial.println(channels[ROLL]);
  // Serial.print(" Y:");
  // Serial.println(channels[YAW]);
  // Serial.print(" A1:");
  // Serial.println(channels[AUX1]);
  // Serial.print(" A2:");
  // Serial.println(channels[AUX2]);
  // Serial.print(" A3(*):");
  // Serial.println(channels[AUX3]);
  /*SerialBT.print(" Rssi:");
  SerialBT.print(rssi);*/

  //SerialBT.print(" Baro alt:");
  SerialBT.println(getBaroAltitude());

  // //SerialBT.print(" Volt:");
  // SerialBT.println(drone_vbat);

  // //SerialBT.print("GyroX: ");
  // SerialBT.println(drone_gyro[0]);

  // //SerialBT.print("GyroY: ");
  // SerialBT.println(drone_gyro[1]);

  // //SerialBT.print("GyroZ: ");
  // SerialBT.println(drone_gyro[2]);

  // //SerialBT.print("AccX: ");
  // SerialBT.println(drone_acc[0]);

  // //SerialBT.print("AccY: ");
  // SerialBT.println(drone_acc[1]);

  // //SerialBT.print("AccZ: ");
  // SerialBT.println(drone_acc[2]); 
}

// Copy BT frame data to channels
void copyBTData(std::array<int16_t, BT_DATA_FRAME_SIZE> buff) {
  // Copy channel data
  for (int i = 0; i < NUM_CHANNELS; i++) {
    channels[i] = buff[i];
  }
  for (int i = NUM_CHANNELS; i < bfs::SbusRx::NUM_CH(); i++) {
    channels[i] = MIN_SBUS_VALUE;
  }
  // Copy rest of the data
  // TODO:
  // Aircraft status, GPS data, altitude data, velocity data, sensor data
}

// Decode data recceived by Bluetooth
int decodeBT() {
  unsigned int b1 = 0;
  unsigned int b2 = 0;
  int val, crc;
  int pk_index = 0;

  // A frame with BT data is comming, we read the channel data from the frame
  while (pk_index <
         BT_DATA_FRAME_SIZE) { // Capture the frame data including the CRC
    if (SerialBT.available()) {
      b1 = SerialBT.read();
      b2 = SerialBT.read();
      val = b2 * 256 + b1;
      if (pk_index < NUM_CHANNELS) // Capture the channel data from the frame
        bt_data[pk_index] = val;
      if (pk_index >= BT_DATA_FRAME_SIZE - 1) { // Last byte on frame is the CRC
        crc = val;
      }
      pk_index = pk_index + 1;
    }
  }
  pk_index = 0;
  return crc;
}

// Compute the CRC from the received frame
int computeCRC(std::array<int16_t, BT_DATA_FRAME_SIZE> buff) {
  int sum1 = 0;
  int sum2 = 0;
  for (int i = 0; i < BT_DATA_FRAME_SIZE - 1; i++) {
    sum1 = (sum1 + buff[i]) % 255;
    sum2 = (sum2 + sum1) % 255;
  }
  return sum1 * 256 + sum2;
}

// Update LED status
void updateLEDStatus() {
  if (system_status != READY_TO_FLIGHT) {
    blinkLED(STARTING_BLINK);
  } else {
    blinkLED(RUNNING_BLINK);
  }
}

//**** Reset channels to minimum value
void resetChannels() {
  for (int i = 0; i < bfs::SbusRx::NUM_CH(); i++) {
    channels[i] = MIN_SBUS_VALUE;
  }
}

// Control the drone
void droneControl() {

  unsigned int b1 = 0;
  unsigned int b2 = 0;
  int val, crc;

  // Update the LED status
  updateLEDStatus();

  showChannelValues();

  // If all devices are connected
  if (system_status == READY_TO_FLIGHT) {

    // Always SBUS is reading from RC commands
    if (sbus_rx.Read() && rc_status == RC_CONNECTED) {
      // Grab the received data
      sbus_data = sbus_rx.ch();
      if (sbus_rx.lost_frame() == false) {
        if (flight_mode ==
            MANUAL_MODE) { // When is in manual mode, all the channels are send
                           // directly to the FC
          sbus_tx.ch(sbus_data);
          // Write the data to the FC
          sbus_tx.Write();
          sBUSToChannel();
          Serial.print("[RC commands] ");
          showChannelValues();
          Serial.println("");
        }
        // Check if flight mode has been changed by RC commands switch
        checkFlightMode(
            sbus_data[AUX3]); // AUX 3 is used to take control of the drone,
                              // this channel is only used by the transmitter
      }
    }

    // Bluetooth reading
    if (flight_mode == AUTONOMOUS_MODE && SerialBT.available()) {

      // Bluettoh decode
      b1 = SerialBT.read();
      b2 = SerialBT.read();
      val = b2 * 256 + b1;
      // This is to prevent getting more frames
      if (bt_status == BT_CONNECTED) {
        if (val == START_BT) {
          if (decodeBT() == computeCRC(bt_data)) {
            copyBTData(bt_data);
            Serial.print("[BT commands] ");
            showChannelValues();
            Serial.println("");
            // Send commands to the FC
            sbus_tx.ch(channels);
            // Write the data to the FC
            sbus_tx.Write();
          }
        }
      }
    }
  } else {
    // Check if the RC data is receiving and it is in not failsafe mode
    if (sbus_rx.Read()) {
      if (sbus_rx.failsafe() != 1) {
        if (rc_status != RC_CONNECTED) {
          rc_status = RC_CONNECTED;
          Serial.println("Transmitter is connected");
        }
      }
    }
    // Bluettoh connection lost is controlled by a callback
  }
  checkConnectionStatus();
}

//**** Telemetry loop
void mspLoop(void *pvParameters) {
  // Update telemetry info
  for (;;) {
    // Get telemetry data
    updateDroneTelem();
    vTaskDelay(10);
  }
}

//**** Main loop
void mainLoop(void *pvParameters) {
  for (;;) {
    droneControl();
    vTaskDelay(10);
  }
}

//**** Not used
void loop() {
  // This delay is important to avoid blocking
  vTaskDelay(10);
}

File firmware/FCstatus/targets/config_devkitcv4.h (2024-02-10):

//Not connected pin
#define NC_PIN 32 

//Pins where the SBUS receiver is connected
#define SBUS_TXPIN 17 //TX2
#define SBUS_RXPIN 16 //RX2

//Pins where the ESP32 Flight controller is used 
#define MSP_TXPIN 23
#define MSP_RXPIN 22

#define LED 2

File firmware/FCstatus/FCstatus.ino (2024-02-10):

#include "Constants.h"
#include "HardwareConfig.h"
#include "MSP.h"

 
// Task
TaskHandle_t mainTask;
TaskHandle_t mspTask;

//MSP port
MSP msp;

void setup() { 
  Serial.begin(BAUDRATE);
  // Waiting for serial
  while (!Serial) {}

  //Init hardware pins
  InitHardwarePins();
  
  //MSP port using Softserial
  Serial2.begin(MSP_BAUDRATE, SERIAL_8N1, MSP_RXPIN, MSP_TXPIN);
  msp.begin(Serial2);
  Serial.println("MSP coomunication started");

  
  // Task to control loops
  // This should be defined at the end because they will car the task functions as soon are defined
  xTaskCreatePinnedToCore(
                    mainLoop,   /* Task function. */
                    "mainLoop",     /* name of task. */
                    10000,       /* Stack size of task */
                    NULL,        /* parameter of the task */
                    1,           /* priority of the task */
                    &mainTask,      /* Task handle to keep track of created task */
                    0);          /* pin task to core 0 */                  
  delay(500); 

  xTaskCreatePinnedToCore(
                    mspLoop,   /* Task function. */
                    "mspLoop",     /* name of task. */
                    10000,       /* Stack size of task */
                    NULL,        /* parameter of the task */
                    1,           /* priority of the task */
                    &mspTask,      /* Task handle to keep track of created task */
                    1);          /* pin task to core 1 */
  delay(500); 


}

// TODO: change these functions 
// Join functions send the same request (faster)
// receive the data to be changed (easy to impement and use)
//int32_t getBaroAltitude(){
//  msp_altitude_t alt;
//  if (msp.request(MSP_ALTITUDE, &alt, sizeof(alt))) {
//     return alt.estimatedActualPosition;
//  }
//  return MSP_INT32_ERROR;
//}
//
//int8_t getVoltage(){
//  msp_analog_t v;
//  if (msp.request(MSP_ANALOG, &v, sizeof(v))){
//     return v.vbat;
//  }
//  return MSP_INT32_ERROR;
//
//}
//
//int8_t getMisc(){
//  msp_misc_t v;
//  if (msp.request(MSP_MISC, &v, sizeof(v))){
//     return v.vbatscale;
//  }
//  return MSP_INT32_ERROR;
//}
//
//int32_t getSonarAltitude(){
//  msp_sonar_altitude_t sonar_alt;
//  if (msp.request(MSP_SONAR_ALTITUDE, &sonar_alt, sizeof(sonar_alt))){
//    return sonar_alt.altitude;
//  }
//  return MSP_INT32_ERROR;
//}
//
//int16_t getGyroX(){
//  msp_raw_imu_t gyro;
//  if (msp.request(MSP_RAW_IMU, &gyro, sizeof(gyro))){
//    return gyro.gyro[0];
//  }
//  return MSP_INT32_ERROR;
//}
//
//int16_t getGyroY(){
//  msp_raw_imu_t gyro;
//  if (msp.request(MSP_RAW_IMU, &gyro, sizeof(gyro))){
//    return gyro.gyro[1];
//  }
//  return MSP_INT32_ERROR;
//}
//
//int16_t getGyroZ(){
//  msp_raw_imu_t gyro;
//  if (msp.request(MSP_RAW_IMU, &gyro, sizeof(gyro))){
//    return gyro.gyro[2];
//  }
//  return MSP_INT32_ERROR;
//}
//
//
//int16_t * getAcc(){
//  msp_raw_imu_t acc;
//  if (msp.request(MSP_RAW_IMU, &acc, sizeof(acc))){
//    return acc.acc;
//  }
//  return MSP_INT32_ERROR;
//}
//
//int16_t getAccY(){
//  msp_raw_imu_t acc;
//  if (msp.request(MSP_RAW_IMU, &acc, sizeof(acc))){
//    return acc.acc[1];
//  }
//  return MSP_INT32_ERROR;
//}
//
//int16_t getAccZ(){
//  msp_raw_imu_t acc;
//  if (msp.request(MSP_RAW_IMU, &acc, sizeof(acc))){
//    return acc.acc[2];
//  }
//  return MSP_INT32_ERROR;
//}


//Get gyro data
bool getGyroData(int16_t rdata[]){
  msp_raw_imu_t gyro;
  if (msp.request(MSP_RAW_IMU, &gyro, sizeof(gyro))){
     rdata[0] = gyro.gyro[0];
     rdata[1] = gyro.gyro[1];
     rdata[2] = gyro.gyro[2];
     return true;
  }
  return false;
}


//Get drone data
void showDroneData(){
    int32_t sonar_alt;
    int8_t vbat;
    int8_t vbatscale;
    int8_t volt;
    int32_t sonar;
    int16_t gyro[3]={0,0,0};
    int16_t acc[3]={0,0,0};

    //Get gyro data
    if(getGyroData(gyro)){
      Serial.print("GyroX: ");
      Serial.print(gyro[0]);
      Serial.print(" GyroY: ");
      Serial.print(gyro[1]);
      Serial.print(" GyroZ: ");
      Serial.println(gyro[2]);
    }
}


// Loop, not used but it should be present
// Known issue https://github.com/espressif/arduino-esp32/issues/595
// https://esp32.com/viewtopic.php?f=2&t=809&p=10191&hilit=esp_task_wdt_feed#p10191
void loop(){
  vTaskDelay(10);
}


// Main loop
void mainLoop(void * pvParameters) {
  for(;;){
    vTaskDelay(10);
  }
}

//Main loop where msp request are
//**** Telemetry loop
void mspLoop(void * pvParameters) {
  for(;;){
    showDroneData();
    vTaskDelay(10);
  }  
}

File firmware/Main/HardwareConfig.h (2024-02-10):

#pragma once

#include <stdint.h>

/// These are all the available targets
#define ESP32DOIT_DEVKIT_V1 1

/// Define the board used
#define BOARD ESP32DOIT_DEVKIT_V1
#define BAUDRATE 115200
//#define MSP_BAUDRATE 9600
#define MSP_BAUDRATE 115200

/// Pins
#define SBUS_TXPIN 17 // TX2
#define SBUS_RXPIN 16 // RX2
#define NC_PIN 32     // Not connected pin

#define MSPTxPin 13
#define MSPRxPin 13
#define LED 9

// Define the aircraft Bluetooth name
// This will be used for the bluetooth name and ssid wifi connection
#define AIRCRAFT_NAME "Drone Droid 01"

// Define the wifi password.
#define WIFI_PASSWORD "testpassword"

/// Outputs all messages on the serial port. Used to use Livetime via USB
#define USE_SERIAL_OUTPUT

// Enables the ArduinoOTA service. It allows flashing over WiFi and enters an
// emergency mode if a crashloop is detected. Comming soon features
//#define USE_ARDUINO_OTA
// defines the time after which the crash loop detection assumes the operation
// is stable
//#define CRASH_COUNT_RESET_TIME_MS 300000

#include "targets/target.h" // Needs to be at the bottom

void InitHardwarePins();
void blinkLED(int);

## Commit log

2024-02-10 Base frame added
    [arm_holder.dxf, bottom_plate.dxf, front_arm.dxf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]
2024-02-10 Sample apps were added
2024-02-12 TPU parts added
    [petg-esp32_holder.stl, petg-fc_protector.stl, tpu-antenna_holder_left.stl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]
